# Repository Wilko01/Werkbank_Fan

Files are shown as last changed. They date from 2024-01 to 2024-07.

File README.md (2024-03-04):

# Fan at workbench
This ESP32 controls the fan of the work bench during welding via the rotary push button at the ESP box. When in local mode the fan of the workbench can be controlled via the rotary push button and when in remote operation the logic in NodeRed is used to reduce the humidity in the shed by operating the fan.

## Description and operation instructions
To operate the fan, the control must be in local mode. This is indicated by a blue led on the ESP. When in remote mode, a green led is lith. When the controls are overridden by a switch then the red LED is lith. The switch is also available as a button in Home Assistant, then the only way to operate the fan is via the buttons in Home Assistant. Switching between local and remote mode is done by pushing the push button. The blue and green leds will light up to indicate the mode. The override button can only be changed via Home Assistant.
In local mode the fan operation is controlled by rotating the rotary push button clockwise to start the fan. The RPM of the fan is indicated from 0 to 100%. Turning counter clockwise will reduce speed. Pushing the rotary push button will turn off the fan immediately.
The fan and the LED display indicates the RPM in %.
In remote mode the fan is turned on when a certain humidity is detected and turned off when it is below another humidity value. Opening or closing the shed door has impact as with an open door it is not logical to run the fan. Hence opening the sheddoor will immediately shut down the fan. The fan is controlled via different levels where at lower humidity levels the fan runs at a lower RPM and when the hunidity level is high the fan runs at a higher RPM. The fan is also turned on when the temperature is very high. The humidity logic is running in NodeRed.

 ## Technical description
A 24V IP65 fan is used as this has a high air volume movement. The 24 voltage is reduced by a mini 360 DC-DC converter to fit a decent voltage of about 7V for the ESP. The DC-DC converter is specified for max 23,5V, but I wonder how tollerant this converter will be. A heatsink is used to reduce the heat of the converter. An DHT11 sensor is used for the temperature and humidity. A 4,7kOhm resistor is used as pull up of the DHT11 data signal.
A NO momentary push button is connected via a 1kOhm resistor to GND. The GPIO is configured as a pull up pin to ensure no false signals.
The EC11 rotary push button is split into 3 connections to the ESP. All 3 have a 1kOhm resistor where the GPIO pins all are configured with an internal pull up. The push action is separated from the rotary and can be treathed as a momentary push button. The rotary function uses pulses and depending on clockwise or counter clockwise it has phase shifted pulses. 
A TM1637 indicates the RPM of the fan in %.
The PWM fan is controlled via the PWM signal coming from the ESP32. A 180Ohm resistor is placed between the GPIO and the PWM connection of the fan. The tacho signal needs a pull up to 3.3V. This could be higher, but the ESP will not accept higher voltages. In practice the 3,3V seems sufficient.
The ESP32 is running ESPHOME and connected to Home Assistant. 
The green and blue LEDs are each connected via a 330Ohm resistor to reduce the max current to 10mA. The red LED is connected via a 220Ohm resistor. All LEDs are configured via a PWM signal. Simply because the ESP has sufficient PWM outputs and this way the light intensity can be controlled.
A (virtual) switch is configured in ESPHome and used as override switch. The switch will be made available in HA automatically. A GPIO pin is needed to configure the switch, but is not used at all. Just use any of the unused pins. In the past I used a Helper in HA, but it is way easier to specify an additional switch in ESPHome as the state us then automatically available in the ESP and kept up to date with HA.

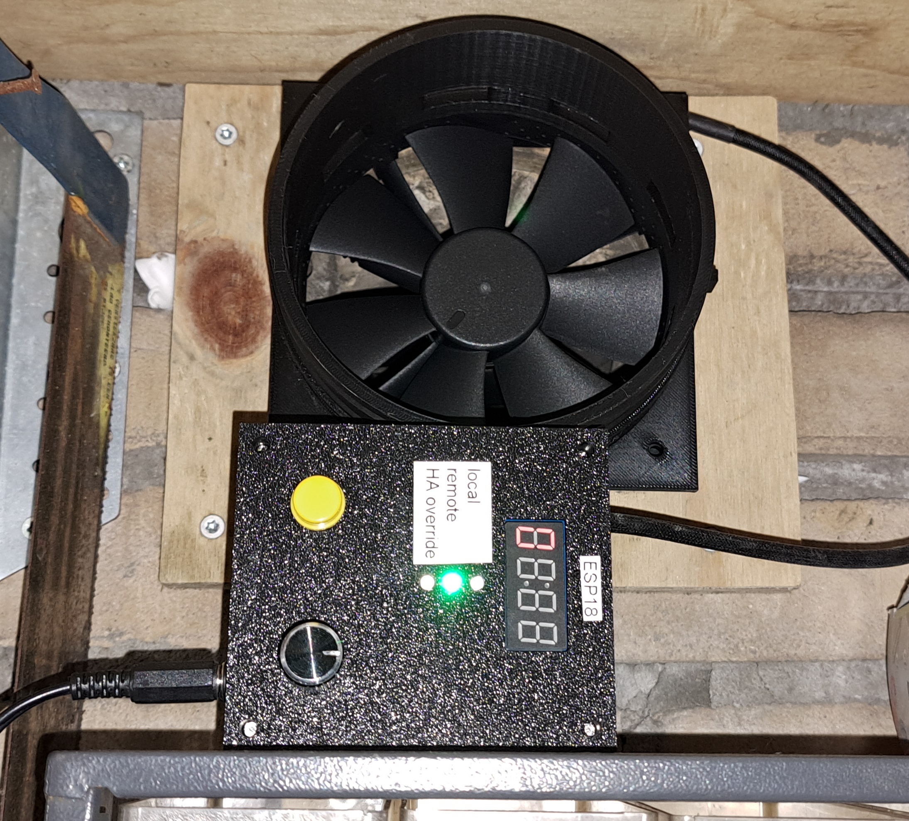
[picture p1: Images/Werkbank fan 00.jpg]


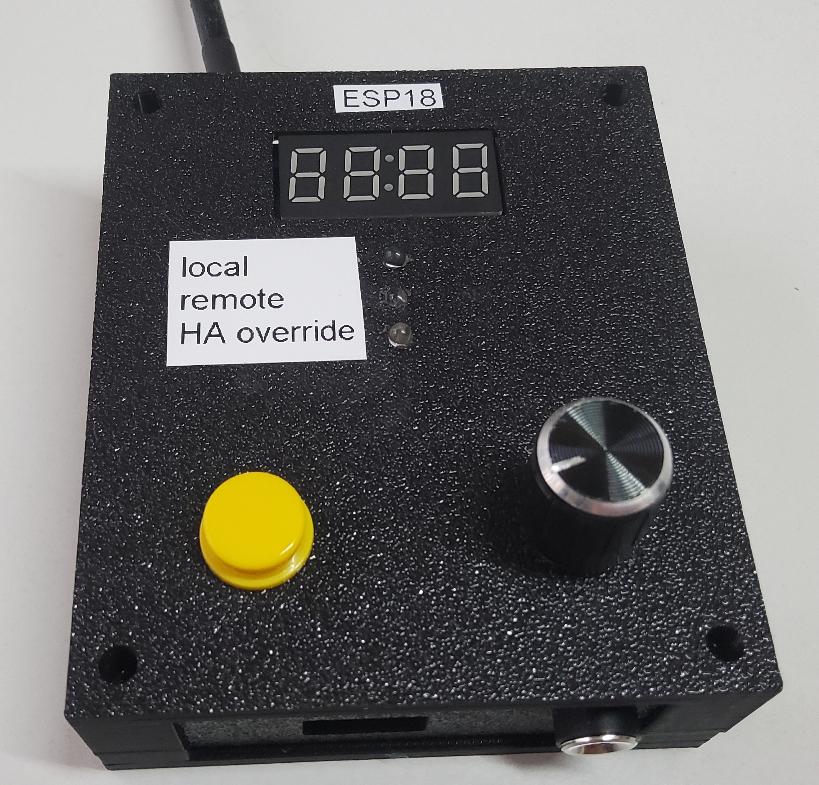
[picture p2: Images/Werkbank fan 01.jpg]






### Parts
1 x ESP32

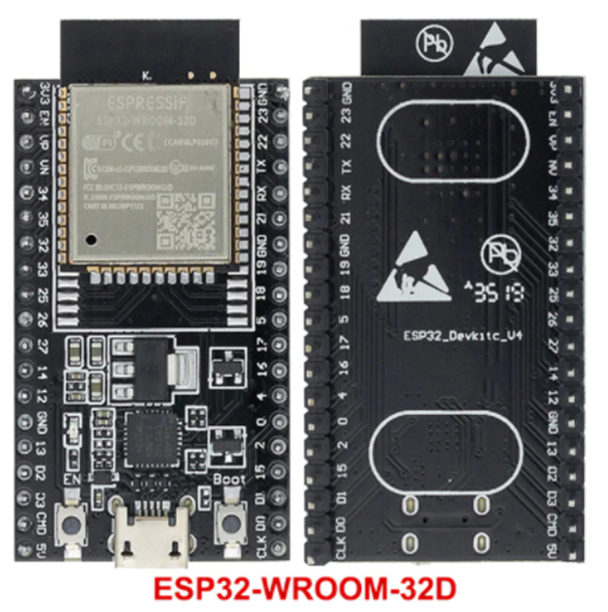
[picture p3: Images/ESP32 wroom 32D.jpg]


1 x DHT11

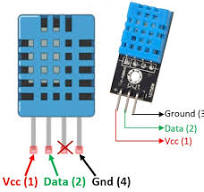
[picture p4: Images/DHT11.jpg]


1 x Fan NF-F12 iPPC-24V-3000 SP IP67 PWM, 120mm

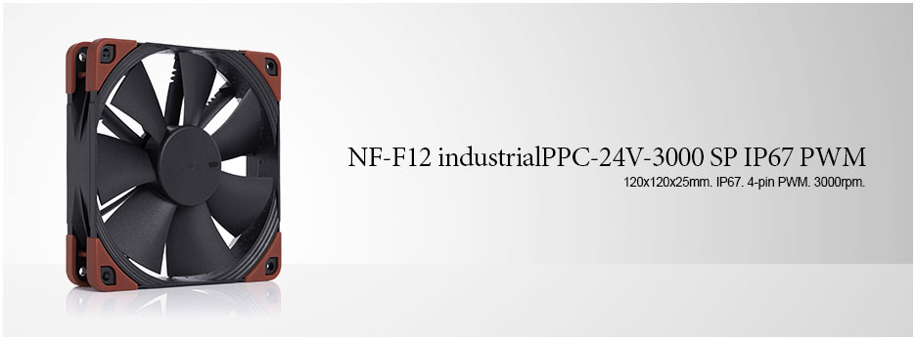
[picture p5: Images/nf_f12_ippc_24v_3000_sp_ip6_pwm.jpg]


Fan pinout pinout

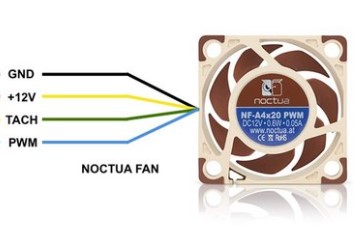
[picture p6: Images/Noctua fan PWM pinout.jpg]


1 x Mini360 DC- DC buck converter

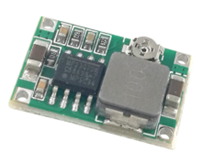
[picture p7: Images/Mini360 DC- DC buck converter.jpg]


1 x TM1637

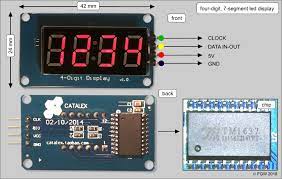
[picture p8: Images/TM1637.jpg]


1 x EC11 Rotary encoder

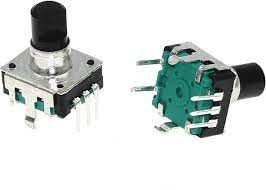
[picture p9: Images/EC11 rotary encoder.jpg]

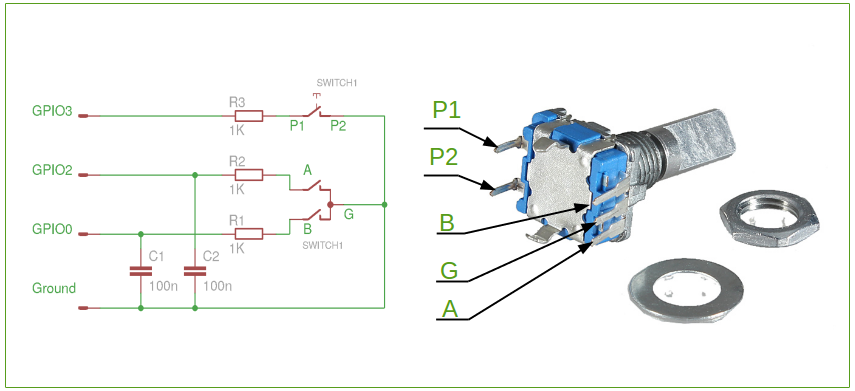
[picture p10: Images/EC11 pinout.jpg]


1 x Push button

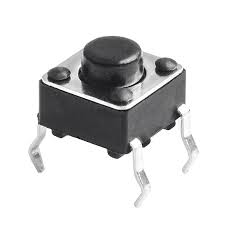
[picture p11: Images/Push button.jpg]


Resistors
1 x 180
1 x 220
2 x 330
4 x 1k
1 x 4k7

LEDs 3mm
1 x Red
1 x Green
1 x Blue

1 x 24V DC adapter

### Schematic overview
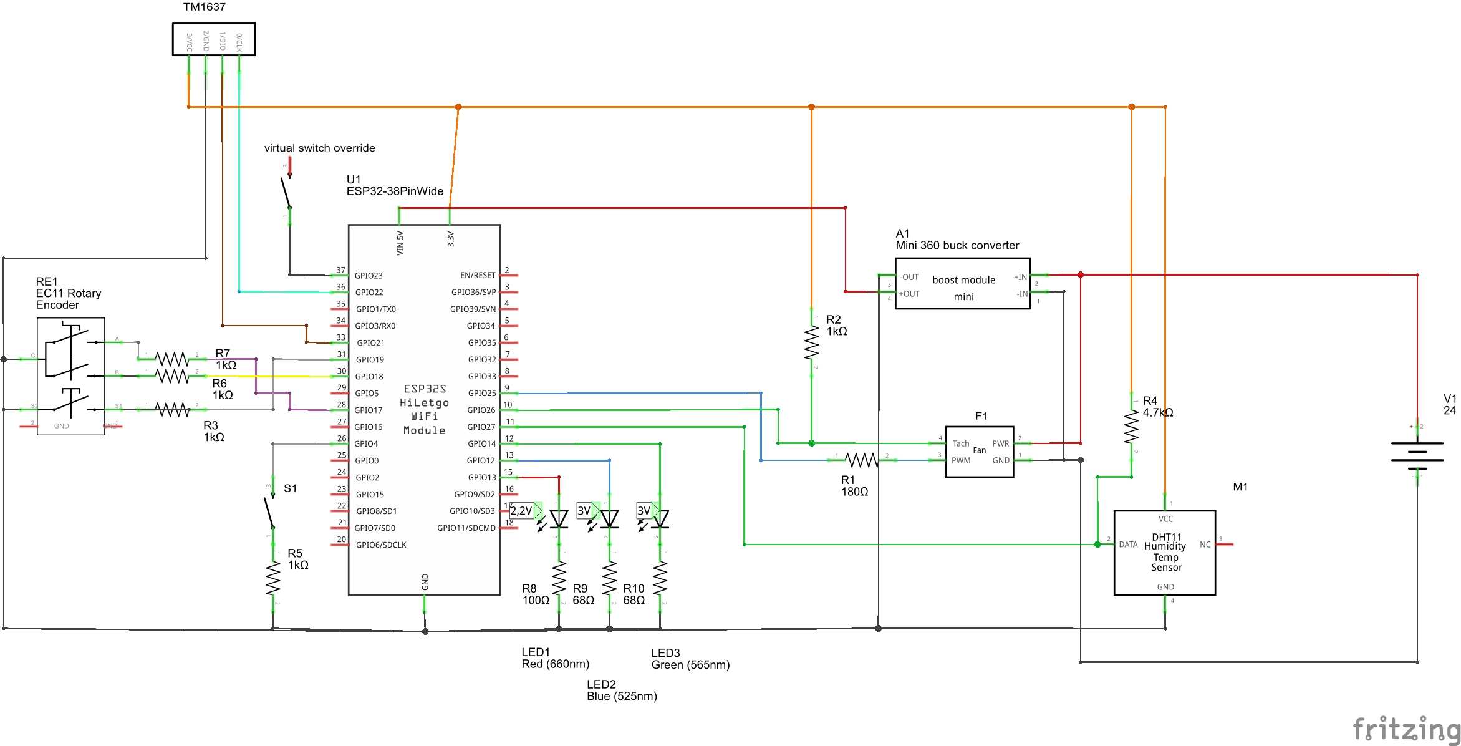
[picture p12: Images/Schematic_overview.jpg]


Note:
•	Power the circuit only via 24V and run code updates via OTA and ESPHOME. When plugging the ESP into the laptop, the amount of current needed is not sufficient

### ESPHOME Configuration
### ESPHome Configuration in Home Assistant
Create a new ESPHOME device with this code:
### Code
[Code in ESPHOME](code.vbs)

## 3D printer files
[3D Printer files](3D_Printer_Files)

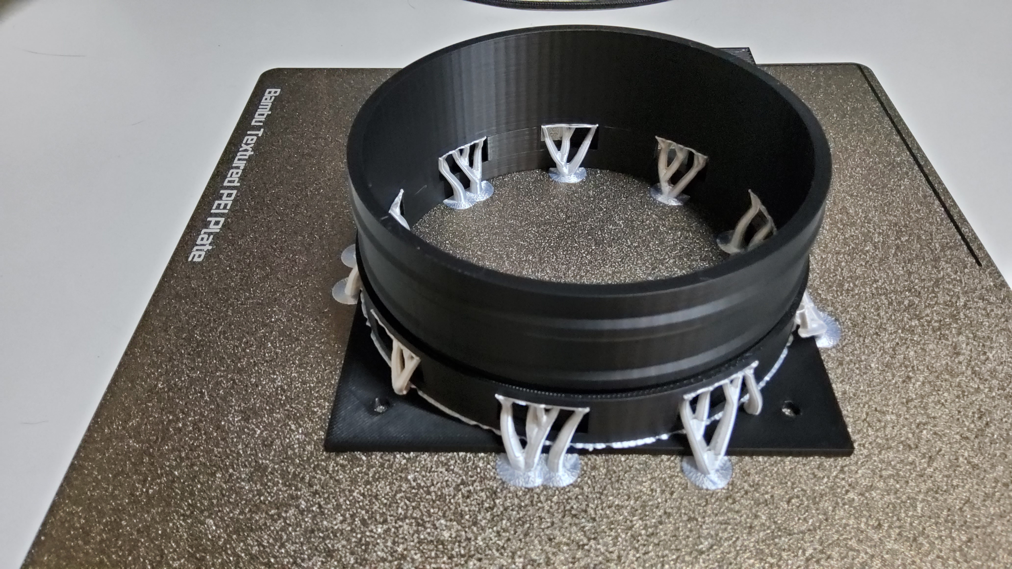
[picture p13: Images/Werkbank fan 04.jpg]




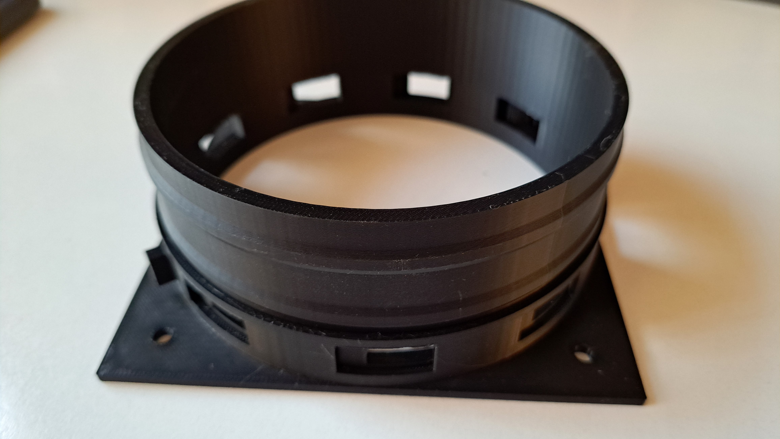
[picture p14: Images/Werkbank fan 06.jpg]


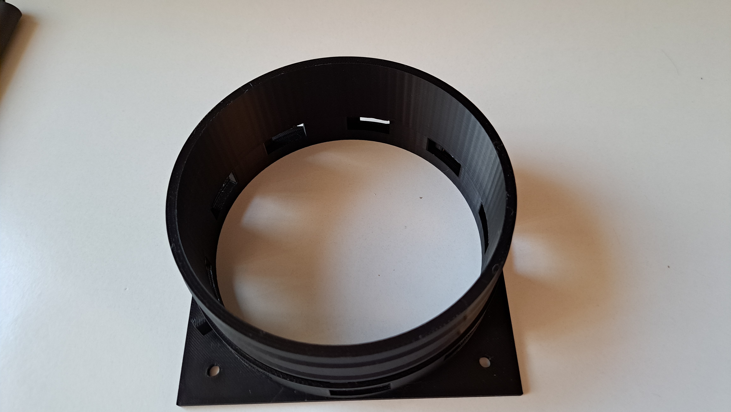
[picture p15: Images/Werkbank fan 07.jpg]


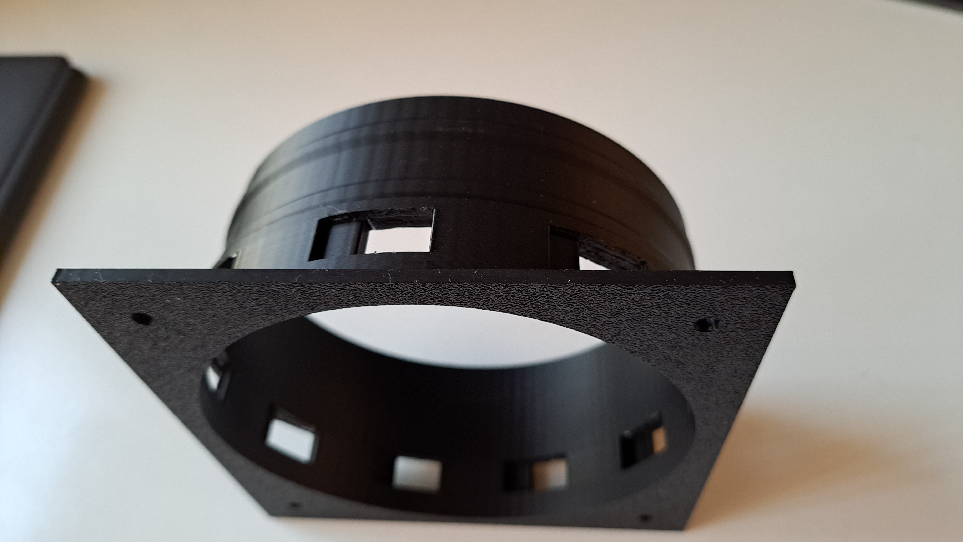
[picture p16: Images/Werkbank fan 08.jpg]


## Open points
The state of the swtiches will nicely be updated when a button is pressed on the ESP. What is not working is the updating of the LED status en RPM % at which the fan runs when controlled locally. I could not yet figure out how to solve the information flow from the ESP to Home Assistant for the LEDs and the RPM of the fan.

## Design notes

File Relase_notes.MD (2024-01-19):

# name of the project

## 2021-12-27 11:08
Copied and pasted the latest code in here
Changed the temperature levels of when to alert and switch the pump on and off

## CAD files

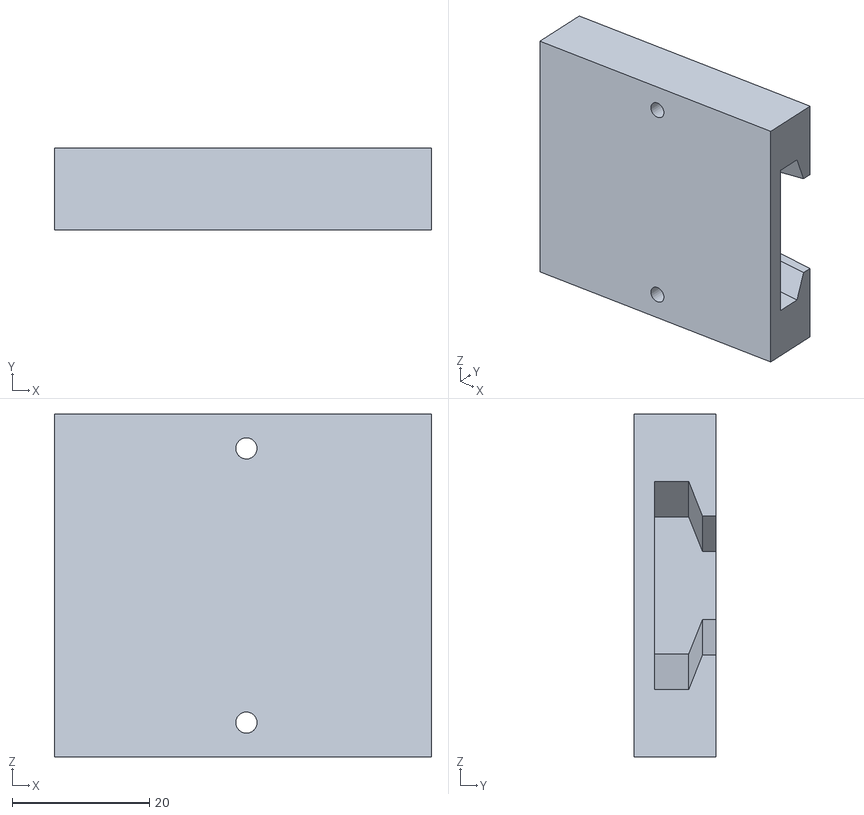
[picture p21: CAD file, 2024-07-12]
3D_Printer_Files/Tube ring connector 03.stl
55.0 x 12.0 x 50.0

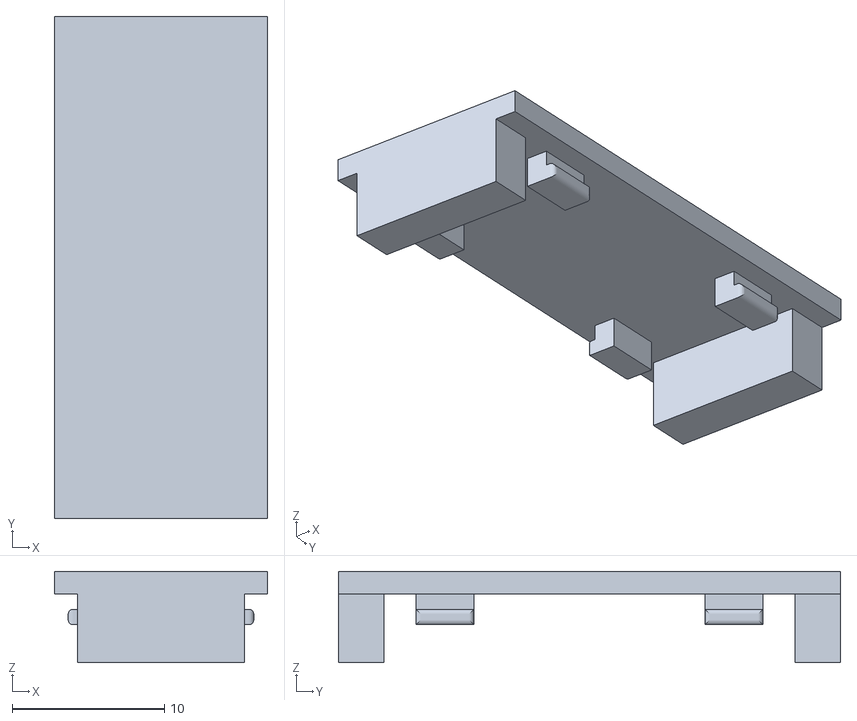
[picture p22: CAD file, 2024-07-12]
3D_Printer_Files/Connector box top 01.stl
14.0 x 33.0 x 6.00

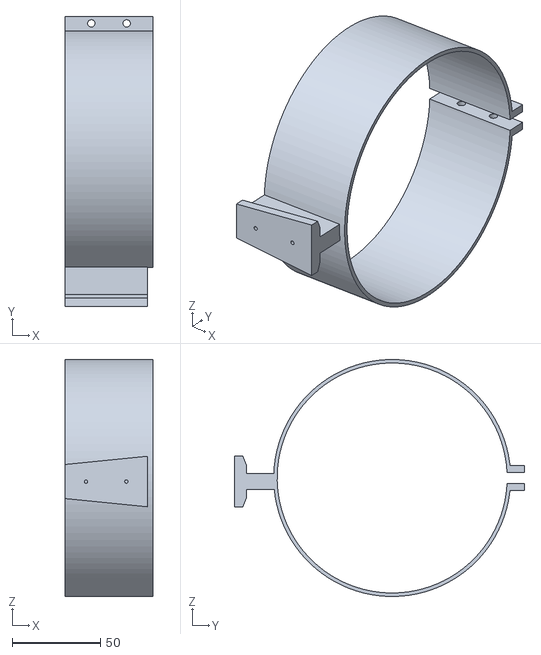
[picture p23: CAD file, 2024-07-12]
3D_Printer_Files/Tube ring 03.stl
50.0 x 164.1 x 134.0

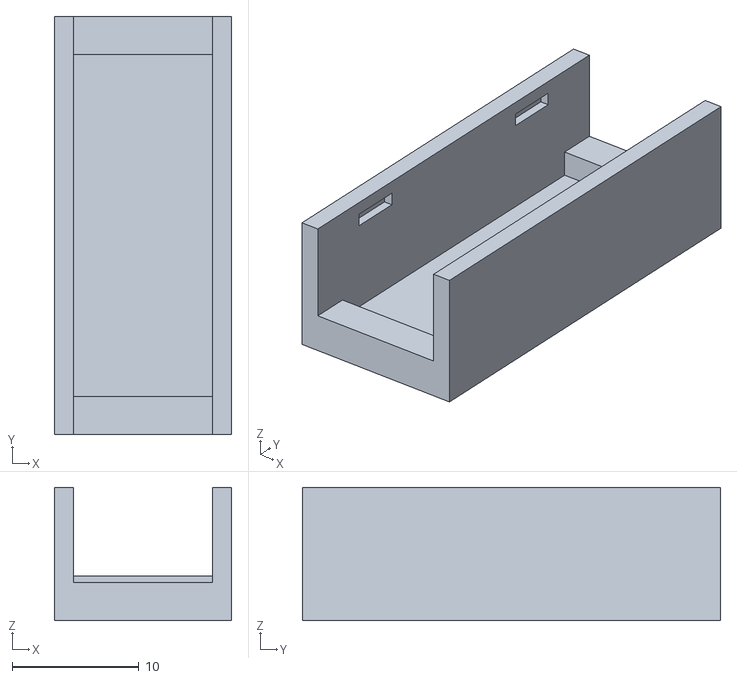
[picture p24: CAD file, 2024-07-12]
3D_Printer_Files/Conncector box bottom 01.stl
14.0 x 33.0 x 10.5

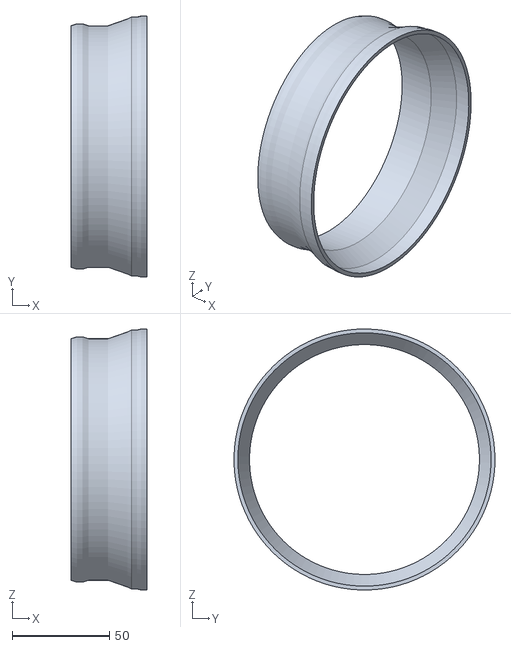
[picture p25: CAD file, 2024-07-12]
3D_Printer_Files/Pipe connector 01.stl
39.0 x 134.0 x 134.0

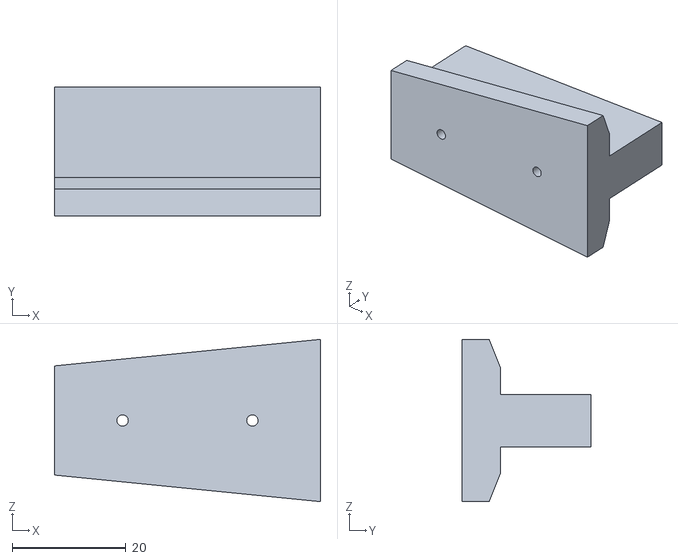
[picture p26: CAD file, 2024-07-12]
3D_Printer_Files/Tube ring connector joint 01.stl
46.9 x 22.8 x 28.6

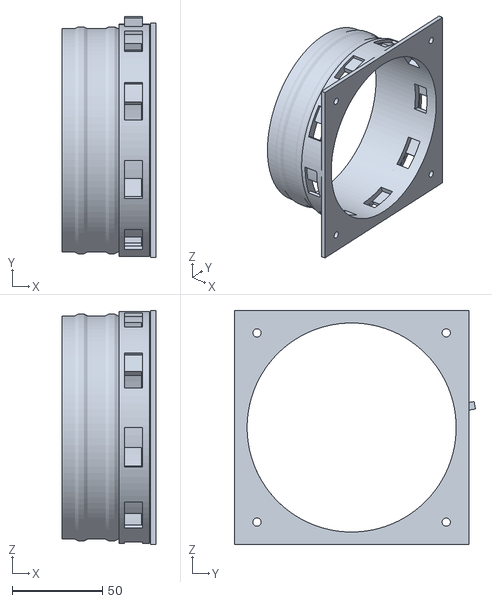
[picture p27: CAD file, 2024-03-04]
3D_Printer_Files/Pipe wall mount 01.stl
52.0 x 133.7 x 130.0

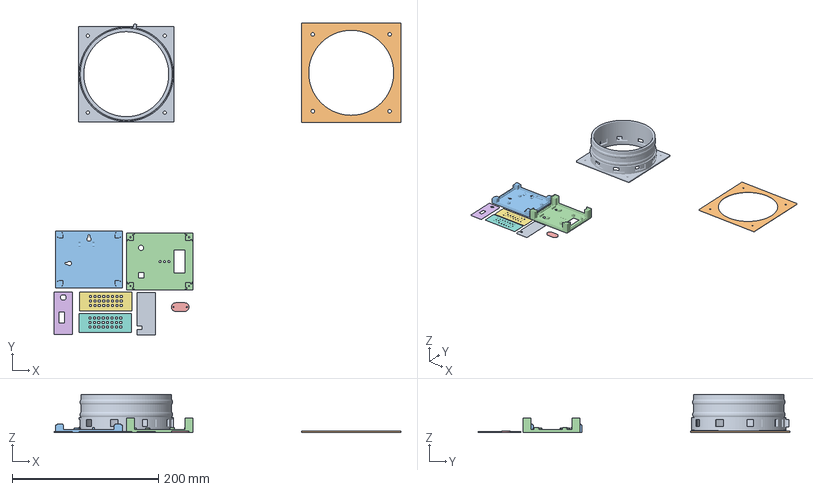
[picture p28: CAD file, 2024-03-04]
3D_Printer_Files/00 All parts 01.3mf
473.9 x 426.1 x 52.0 mm
Pipe wall mount 01.stl
Seal for fan 01.stl
Box Bottom 01.stl
Box Top 01.stl
Button lock plate 01.stl
Side bottom.stl
Side left and right.stl x 2
Side top.stl

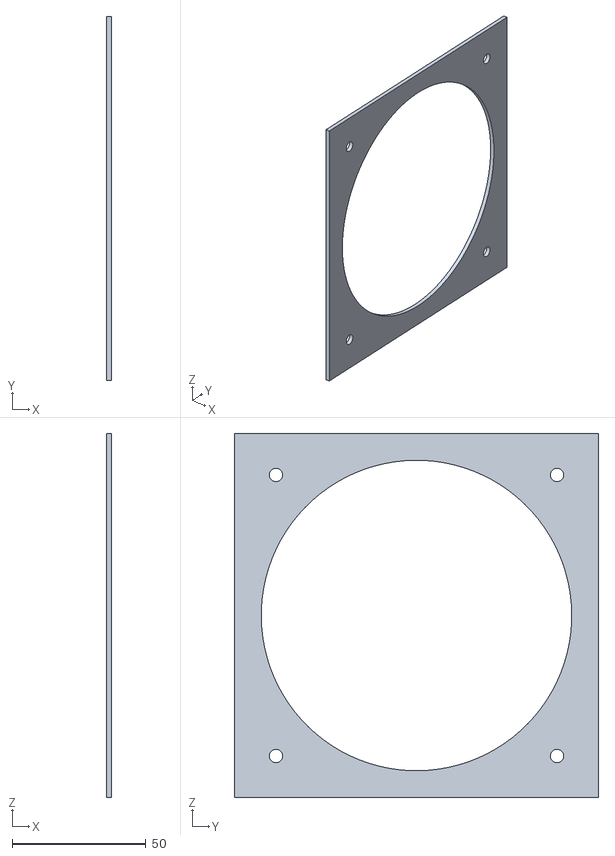
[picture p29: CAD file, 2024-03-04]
3D_Printer_Files/Seal for fan 01.stl
2.00 x 136.0 x 136.0

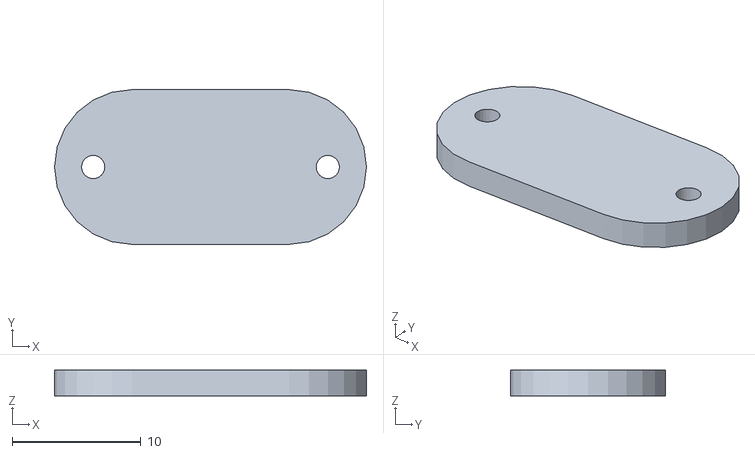
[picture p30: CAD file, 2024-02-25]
3D_Printer_Files/Button lock plate 01.stl
24.2 x 12.0 x 2.00

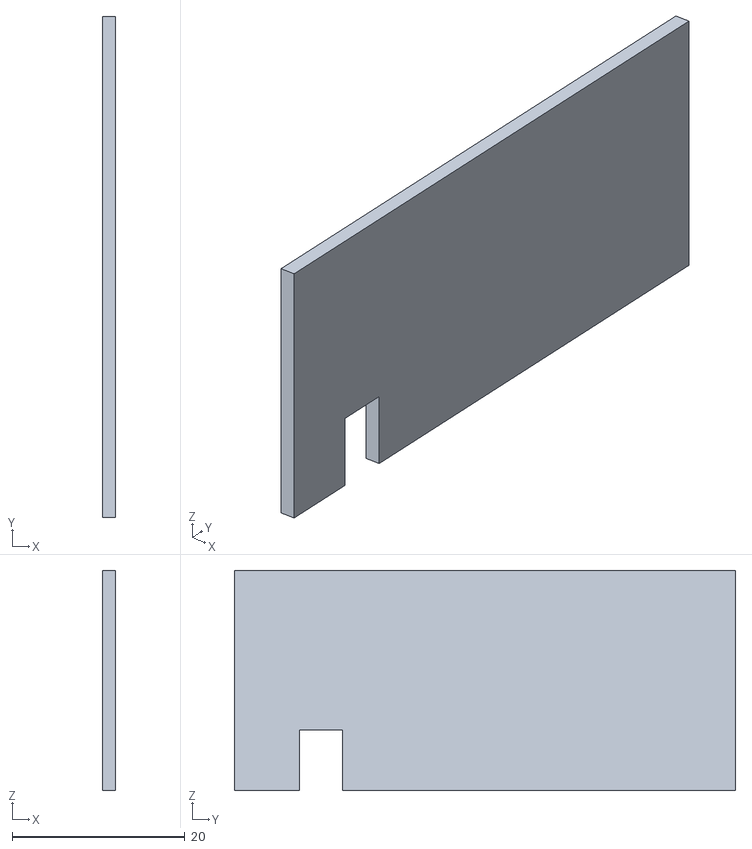
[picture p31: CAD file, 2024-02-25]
3D_Printer_Files/Side top.stl
1.50 x 58.0 x 25.5

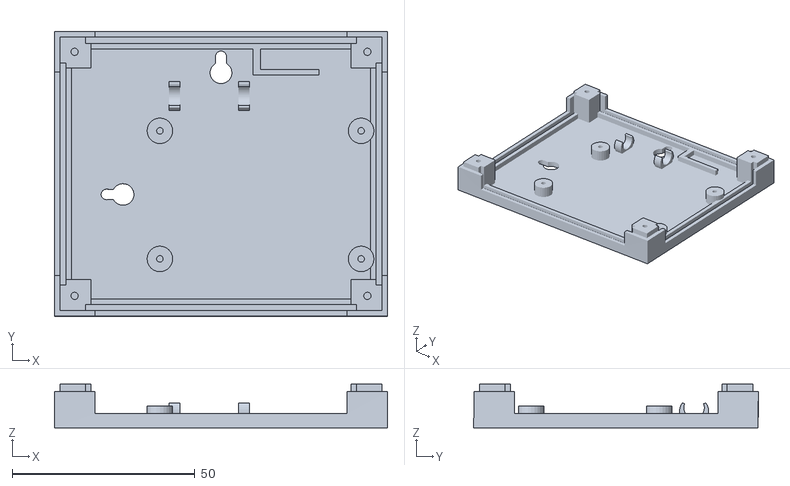
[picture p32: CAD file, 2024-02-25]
3D_Printer_Files/Box Bottom 01.stl
91.0 x 77.8 x 12.0

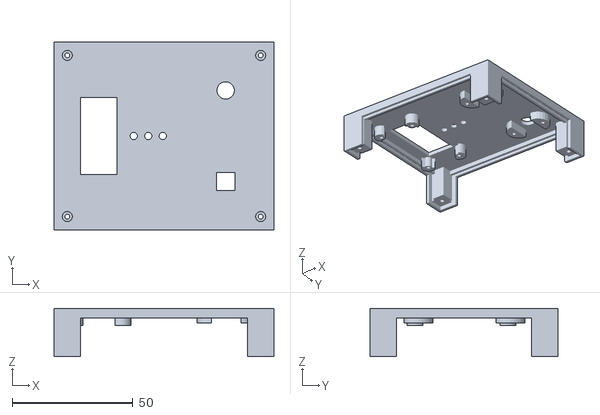
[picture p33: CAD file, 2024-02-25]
3D_Printer_Files/Box Top 01.stl
91.0 x 77.7 x 20.0

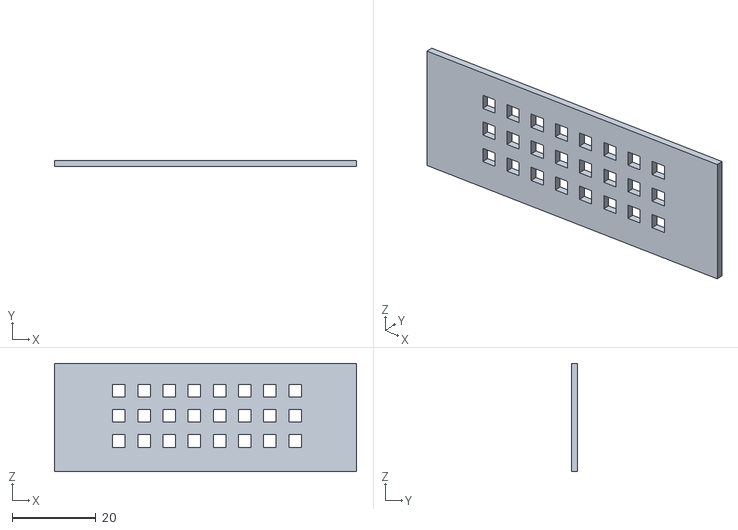
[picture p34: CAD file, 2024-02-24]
3D_Printer_Files/Side left and right.stl
72.0 x 1.50 x 25.8

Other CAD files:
3D_Printer_Files/Side bottom.stl

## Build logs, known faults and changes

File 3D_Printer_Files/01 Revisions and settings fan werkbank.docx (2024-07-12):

# Print settings:

- Print material: PLA and TPU
- Rotation of the objects: No comment.
- Support: No
- Skirt, brim: Skirt.
- Infill: 50% for PLA and 20% for TPU
- Print the ‘Inner fan ceiling mount 01’ with the side of the pipe connection at the building plate so the parts where the magnets are located doesn’t need support.

# Additional instructions

- None

# Materials needed

- Filament. Started with ABS, but the adhesive between the layers of the used ABS was not strong and therefore switched to PLA

# Log history

# Version 0.3

- The connection of the ring to the pipe connector is too detailed which results in a very accurate placing. To reduce this I made a more raw connector
- The fitting of the tube to the pipe wall mount is not smooth and therefor a pipe connector is made

# Version 0.2

- Did not print it yet and I’m not going to as the ring is shifting a bit stiff at the moment. Not sure why. Potentially due to moisture or temperature as the parts are now installed in the shed
- Tighten the ring slightly by reducing the diameter of the ring with 0.5mm

# Version 0.1

- First release
- The print with the specific PLA support worked great. The support at the ring of the fan mount could easily be removed. A future version of the ring may be a little more tight as due to vibrations of the fan mount the ring could be moving

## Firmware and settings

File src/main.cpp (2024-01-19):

#include <Arduino.h>

// put function declarations here:
int myFunction(int, int);

void setup() {
  // put your setup code here, to run once:
  int result = myFunction(2, 3);
}

void loop() {
  // put your main code here, to run repeatedly:
}

// put function definitions here:
int myFunction(int x, int y) {
  return x + y;
}

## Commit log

2024-01-19 Initial fill
    [Connection fan 03.stl, Schematic overview.fzz]
2024-02-12 Fan and rotaty working
    [Schematic overview 01.fzz, Schematic overview 02.fzz, Schematic overview.fzz]
2024-02-13 Update description
    [Schematic overview 02.fzz, Schematic overview 03.fzz]
2024-02-25 first release
    [Box Bottom 01.stl, Box Top 01.stl, Button lock plate 01.stl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]
2024-03-10 update annotation in the code and 3D files
    [Tube ring 02.stl, Tube ring connector 02.stl]
